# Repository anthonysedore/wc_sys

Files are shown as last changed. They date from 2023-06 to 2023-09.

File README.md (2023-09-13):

# wc_sys
Wireless Communication System for Electrathon





PCB designed in KiCad,

Code for ESP32 in Arduino

-read data from motor controller, battery BMS
-collect GPS data
-log all data to sdcard
-send data to pitcrew
-show important metrics and any warnings to driver
-enable recording cool videos with data synced to video time

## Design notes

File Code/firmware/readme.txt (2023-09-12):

freeRTOS and freeRTOS_geneisboard is the firmware going onto the board.
They should be combined but kept seperate for now, since pinout is different.

Do development in freeRTOS not freeRTOS_geneisboard

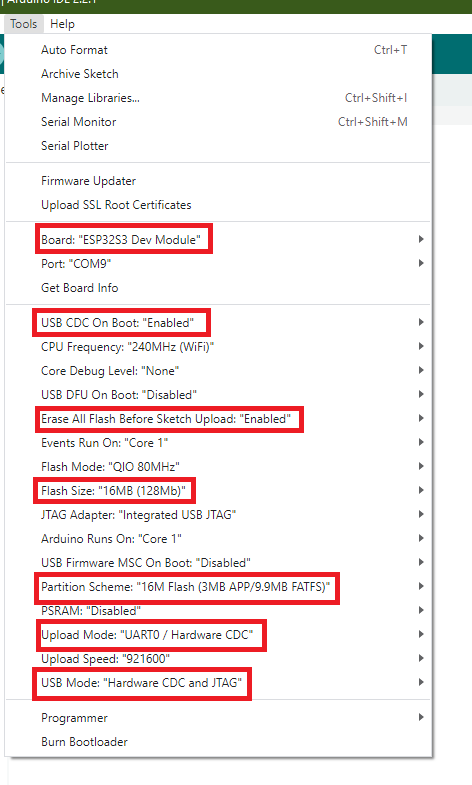
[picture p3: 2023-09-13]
Code/genesisboard.png

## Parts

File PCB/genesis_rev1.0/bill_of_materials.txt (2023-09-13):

"P/N	price	qty	description	notes"	
"PCB	26.9	5	from JLCPCB	"	
"MCP23008-E/SO-ND	$1.37 	1	IC XPNDR 1.7MHZ I2C 18SOIC	"	
"CP-43514-ND	$1.32 	1	CONN JACK 4COND 3.5MM R/A	""wrong jack for board"	" order new one"""
"497-5235-1-ND	$0.61 	1	TVS DIODE 5.25VWM 17VC SOT23-6	"	
"2073-USB4105-GF-ACT-ND	$0.81 	1	CONN RCP USB2.0 TYP C 24P SMD RA	"	
"EG4367-ND	$1.04 	1	SWITCH SLIDE DPDT 500MA 15V	"	
"PI4ULS5V202UEXDICT-ND	$0.76 	2	IC TRANSLTR BIDIRECTIONAL 8MSOP	"	
"DMG2301L-7DICT-ND	$0.33 	1	MOSFET P-CH 20V 3A SOT23	"	
"MCP73831T-2ACI/OTCT-ND	$0.76 	1	IC BATT CNTL LI-ION 1CEL SOT23-5	"	
"1965-ESP32-S3-WROOM-1U-N16R8CT-ND	$3.90 	1	RF TXRX MOD BLUETOOTH U.FL SMD	"
"hosyond3.5tft	$17	1	Hosyond 3.5 Inches TFT LCD Touch Screen	"
"neo-6m	$11	1	GPS Module GPS NEO-6M	"

about cost, $44 for a board
other parts that are not listed I had lying around should as resistors and capacitors, should document

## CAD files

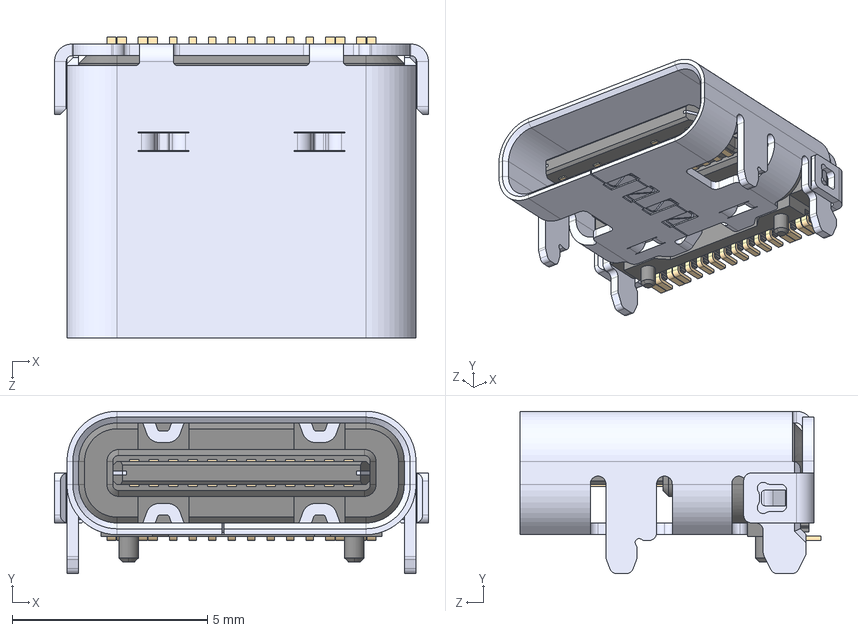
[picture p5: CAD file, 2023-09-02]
PCB/wc_sys_footprint/3dmodels/USB4105-GF-A.step
9.58 x 4.16 x 7.71 mm

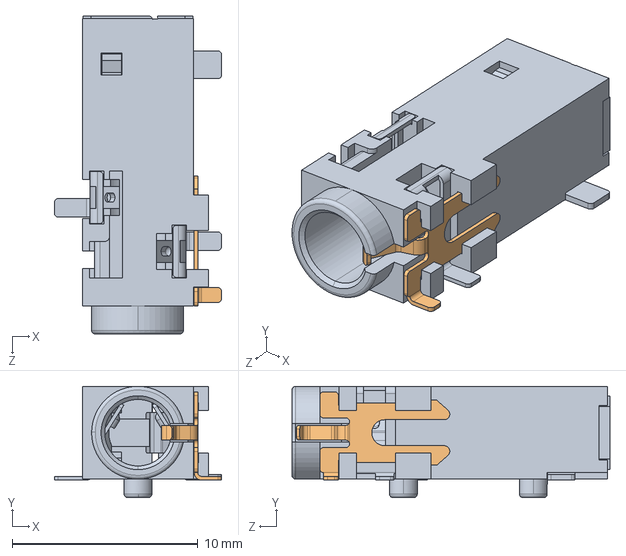
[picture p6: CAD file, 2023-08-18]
PCB/wc_sys_footprint/3dmodels/CUI_DEVICES_SJ-43514-SMT-TR.step
9.00 x 6.00 x 17.1 mm

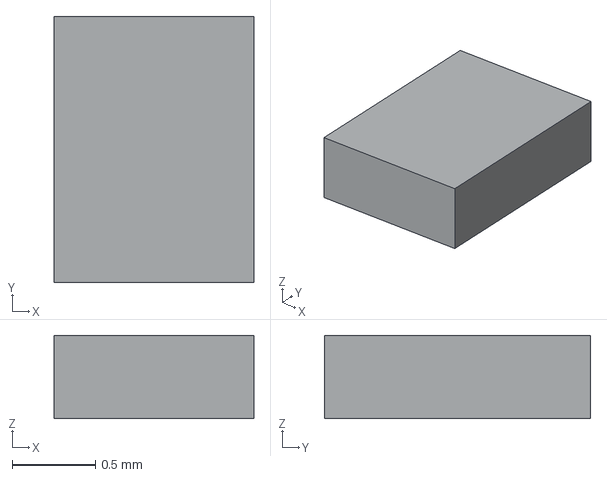
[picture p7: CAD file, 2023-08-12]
PCB/wc_sys_footprint/3dmodels/PI4ULS5V202XVEX.step
1.20 x 1.60 x 0.5 mm

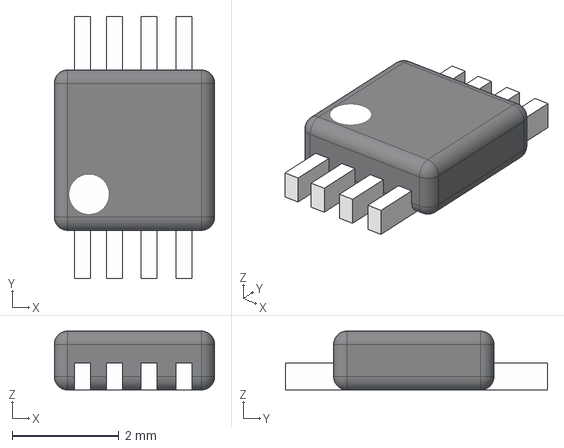
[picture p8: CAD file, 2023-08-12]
PCB/wc_sys_footprint/3dmodels/PI4ULS5V202UEX.step
3.00 x 4.90 x 1.10 mm

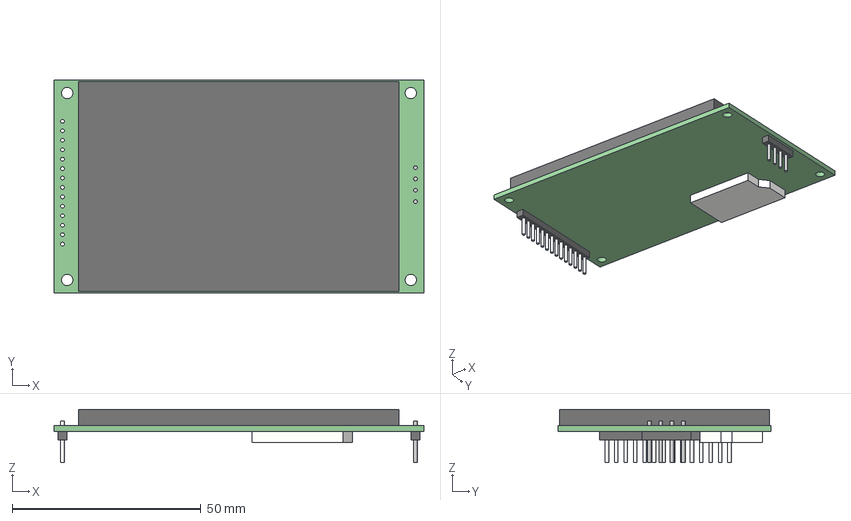
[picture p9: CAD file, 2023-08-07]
PCB/wc_sys_footprint/3dmodels/LCD Display.step
98.0 x 56.5 x 14.1 mm

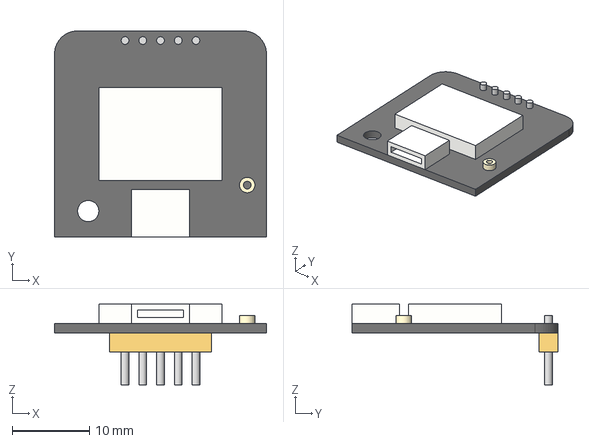
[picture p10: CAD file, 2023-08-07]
PCB/wc_sys_footprint/3dmodels/GT-U7GpsModule v1.step
27.5 x 26.8 x 10.5 mm

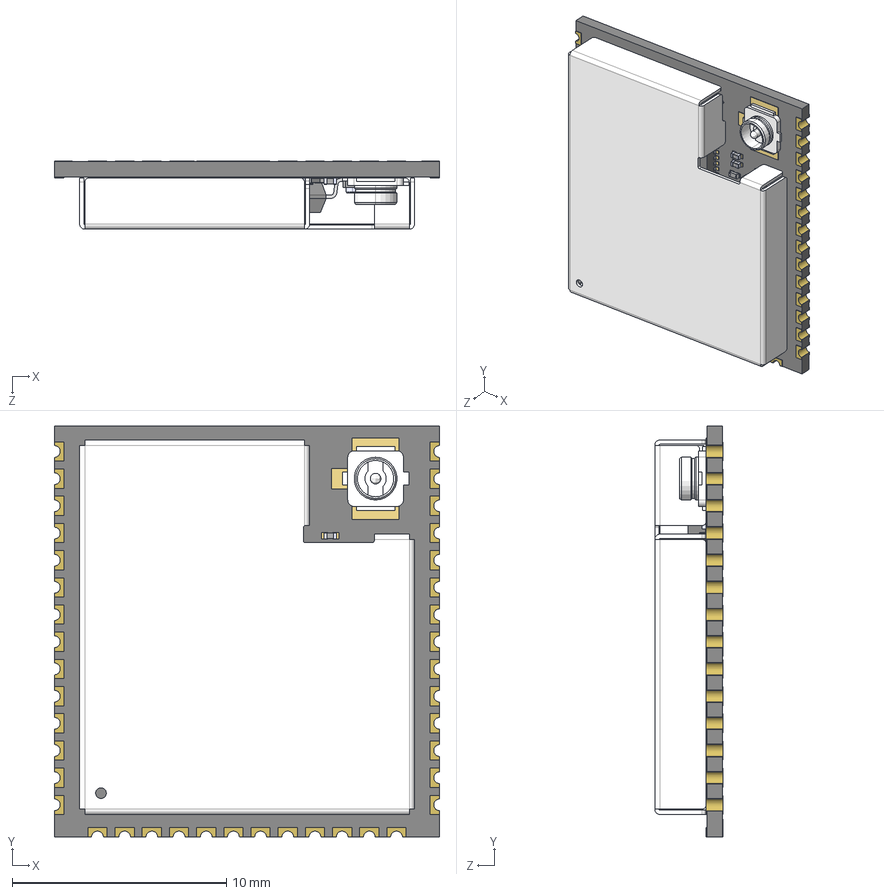
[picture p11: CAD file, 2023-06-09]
PCB/wc_sys_footprint/3dmodels/ESP32-S3-WROOM-1U.STEP
18.0 x 19.2 x 3.20 mm
R0201_20210301.STEP^R0201_20210301.STEP_Submodel-R0201_part_DesignRootModel_ESP32-S3-WROOM-1U(2)_ESP32-S3-WROOM-1U_2 x 8
L0201_20210301.STEP^L0201_20210301.STEP_Submodel-L0201_part_DesignRootModel_ESP32-S3-WROOM-1U(2)_ESP32-S3-WROOM-1U_2 x 2
C0201_20210301.STEP^C0201_20210301.STEP_Submodel-C0201_part_DesignRootModel_ESP32-S3-WROOM-1U(2)_ESP32-S3-WROOM-1U_2 x 13
C0402_20210301.STEP^C0402_20210301.STEP_Submodel-C0402_part_DesignRootModel_ESP32-S3-WROOM-1U(2)_ESP32-S3-WROOM-1U_2
I-IPEX.STEP^I-IPEX.STEP_Submodel-IPEX_3P_part_DesignRootModel_ESP32-S3-WROOM-1U(2)_ESP32-S3-WROOM-1U_2
DFN1006.STEP^DFN1006.STEP_Submodel-SOD882_part_DesignRootModel_ESP32-S3-WROOM-1U(2)_ESP32-S3-WROOM-1U_2
SOP8_rev1_20210308.STEP^SOP8_rev1_20210308.STEP_Submodel-SOP8_1P27_6P6_part_DesignRootModel_ESP32-S3-WROOM-1U(2)_ESP32-S3-WROOM-1U_2
ESP32-S3_20210301.STEP^ESP32-S3_20210301.STEP_Submodel-QFN56_0P4_7_part_DesignRootModel_ESP32-S3-WROOM-1U(2)_ESP32-S3-WROOM-1U_2
XTAL3225_20210301.STEP^XTAL3225_20210301.STEP_Submodel-XTAL3225_part_DesignRootModel_ESP32-S3-WROOM-1U(2)_ESP32-S3-WROOM-1U_2
uid__4-111^DesignRootModel_ESP32-S3-WROOM-1U(2)_ESP32-S3-WROOM-1U_2
uid__4-112^DesignRootModel_ESP32-S3-WROOM-1U(2)_ESP32-S3-WROOM-1U_2
uid__4-113^DesignRootModel_ESP32-S3-WROOM-1U(2)_ESP32-S3-WROOM-1U_2
uid__4-130^DesignRootModel_ESP32-S3-WROOM-1U(2)_ESP32-S3-WROOM-1U_2
uid__4-131^DesignRootModel_ESP32-S3-WROOM-1U(2)_ESP32-S3-WROOM-1U_2
uid__4-132^DesignRootModel_ESP32-S3-WROOM-1U(2)_ESP32-S3-WROOM-1U_2
uid__4-148^DesignRootModel_ESP32-S3-WROOM-1U(2)_ESP32-S3-WROOM-1U_2
uid__4-149^DesignRootModel_ESP32-S3-WROOM-1U(2)_ESP32-S3-WROOM-1U_2
uid__4-150^DesignRootModel_ESP32-S3-WROOM-1U(2)_ESP32-S3-WROOM-1U_2
uid__1-253^DesignRootModel_ESP32-S3-WROOM-1U(2)_ESP32-S3-WROOM-1U_2
uid__1-254^DesignRootModel_ESP32-S3-WROOM-1U(2)_ESP32-S3-WROOM-1U_2
uid__1-256^DesignRootModel_ESP32-S3-WROOM-1U(2)_ESP32-S3-WROOM-1U_2
uid__1-257^DesignRootModel_ESP32-S3-WROOM-1U(2)_ESP32-S3-WROOM-1U_2
uid__1-266^DesignRootModel_ESP32-S3-WROOM-1U(2)_ESP32-S3-WROOM-1U_2
uid__1-269^DesignRootModel_ESP32-S3-WROOM-1U(2)_ESP32-S3-WROOM-1U_2
uid__1-270^DesignRootModel_ESP32-S3-WROOM-1U(2)_ESP32-S3-WROOM-1U_2
uid__1-271^DesignRootModel_ESP32-S3-WROOM-1U(2)_ESP32-S3-WROOM-1U_2
uid__1-272^DesignRootModel_ESP32-S3-WROOM-1U(2)_ESP32-S3-WROOM-1U_2
uid__1-273^DesignRootModel_ESP32-S3-WROOM-1U(2)_ESP32-S3-WROOM-1U_2
uid__1-274^DesignRootModel_ESP32-S3-WROOM-1U(2)_ESP32-S3-WROOM-1U_2
uid__1-275^DesignRootModel_ESP32-S3-WROOM-1U(2)_ESP32-S3-WROOM-1U_2
uid__1-276^DesignRootModel_ESP32-S3-WROOM-1U(2)_ESP32-S3-WROOM-1U_2
uid__1-277^DesignRootModel_ESP32-S3-WROOM-1U(2)_ESP32-S3-WROOM-1U_2
uid__1-280^DesignRootModel_ESP32-S3-WROOM-1U(2)_ESP32-S3-WROOM-1U_2
uid__1-292^DesignRootModel_ESP32-S3-WROOM-1U(2)_ESP32-S3-WROOM-1U_2
uid__1-293^DesignRootModel_ESP32-S3-WROOM-1U(2)_ESP32-S3-WROOM-1U_2
uid__1-297^DesignRootModel_ESP32-S3-WROOM-1U(2)_ESP32-S3-WROOM-1U_2
uid__1-300^DesignRootModel_ESP32-S3-WROOM-1U(2)_ESP32-S3-WROOM-1U_2
uid__1-301^DesignRootModel_ESP32-S3-WROOM-1U(2)_ESP32-S3-WROOM-1U_2
uid__1-302^DesignRootModel_ESP32-S3-WROOM-1U(2)_ESP32-S3-WROOM-1U_2
uid__1-303^DesignRootModel_ESP32-S3-WROOM-1U(2)_ESP32-S3-WROOM-1U_2
uid__1-307^DesignRootModel_ESP32-S3-WROOM-1U(2)_ESP32-S3-WROOM-1U_2
uid__1-313^DesignRootModel_ESP32-S3-WROOM-1U(2)_ESP32-S3-WROOM-1U_2
uid__1-319^DesignRootModel_ESP32-S3-WROOM-1U(2)_ESP32-S3-WROOM-1U_2
uid__1-320^DesignRootModel_ESP32-S3-WROOM-1U(2)_ESP32-S3-WROOM-1U_2
uid__1-321^DesignRootModel_ESP32-S3-WROOM-1U(2)_ESP32-S3-WROOM-1U_2
uid__1-328^DesignRootModel_ESP32-S3-WROOM-1U(2)_ESP32-S3-WROOM-1U_2
uid__1-332^DesignRootModel_ESP32-S3-WROOM-1U(2)_ESP32-S3-WROOM-1U_2
uid__1-333^DesignRootModel_ESP32-S3-WROOM-1U(2)_ESP32-S3-WROOM-1U_2
uid__1-334^DesignRootModel_ESP32-S3-WROOM-1U(2)_ESP32-S3-WROOM-1U_2
uid__1-335^DesignRootModel_ESP32-S3-WROOM-1U(2)_ESP32-S3-WROOM-1U_2
uid__1-336^DesignRootModel_ESP32-S3-WROOM-1U(2)_ESP32-S3-WROOM-1U_2
uid__1-337^DesignRootModel_ESP32-S3-WROOM-1U(2)_ESP32-S3-WROOM-1U_2
uid__1-338^DesignRootModel_ESP32-S3-WROOM-1U(2)_ESP32-S3-WROOM-1U_2
uid__1-339^DesignRootModel_ESP32-S3-WROOM-1U(2)_ESP32-S3-WROOM-1U_2
uid__1-340^DesignRootModel_ESP32-S3-WROOM-1U(2)_ESP32-S3-WROOM-1U_2
uid__1-341^DesignRootModel_ESP32-S3-WROOM-1U(2)_ESP32-S3-WROOM-1U_2
uid__1-342^DesignRootModel_ESP32-S3-WROOM-1U(2)_ESP32-S3-WROOM-1U_2
uid__1-343^DesignRootModel_ESP32-S3-WROOM-1U(2)_ESP32-S3-WROOM-1U_2
uid__1-344^DesignRootModel_ESP32-S3-WROOM-1U(2)_ESP32-S3-WROOM-1U_2
uid__1-345^DesignRootModel_ESP32-S3-WROOM-1U(2)_ESP32-S3-WROOM-1U_2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

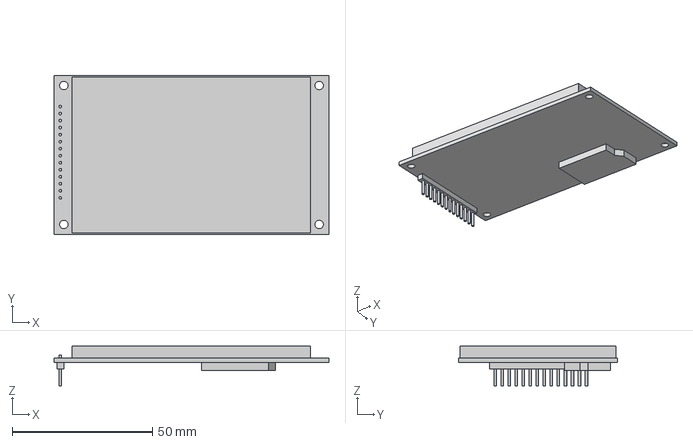
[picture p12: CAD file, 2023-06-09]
PCB/wc_sys_footprint/3dmodels/3.5 TFI SPI 480X320 V1 v3.step
98.0 x 56.5 x 14.1 mm

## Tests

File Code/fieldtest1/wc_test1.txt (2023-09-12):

csv file is direct output from SDcard mounted in unit.
Video created in racerender using gopro video and csv file output.
-------
set gps sample rate higher
fix crash when gps doesn't pick up satelite and try to start recording
improve time syncronization instead of relying on delays

investigate if SDcard should go on seperate SPI controller on esp32

Add GOPRO control feature to start and stop recording automatically

--------------------
Update: gps sample rate and fixed time sync.

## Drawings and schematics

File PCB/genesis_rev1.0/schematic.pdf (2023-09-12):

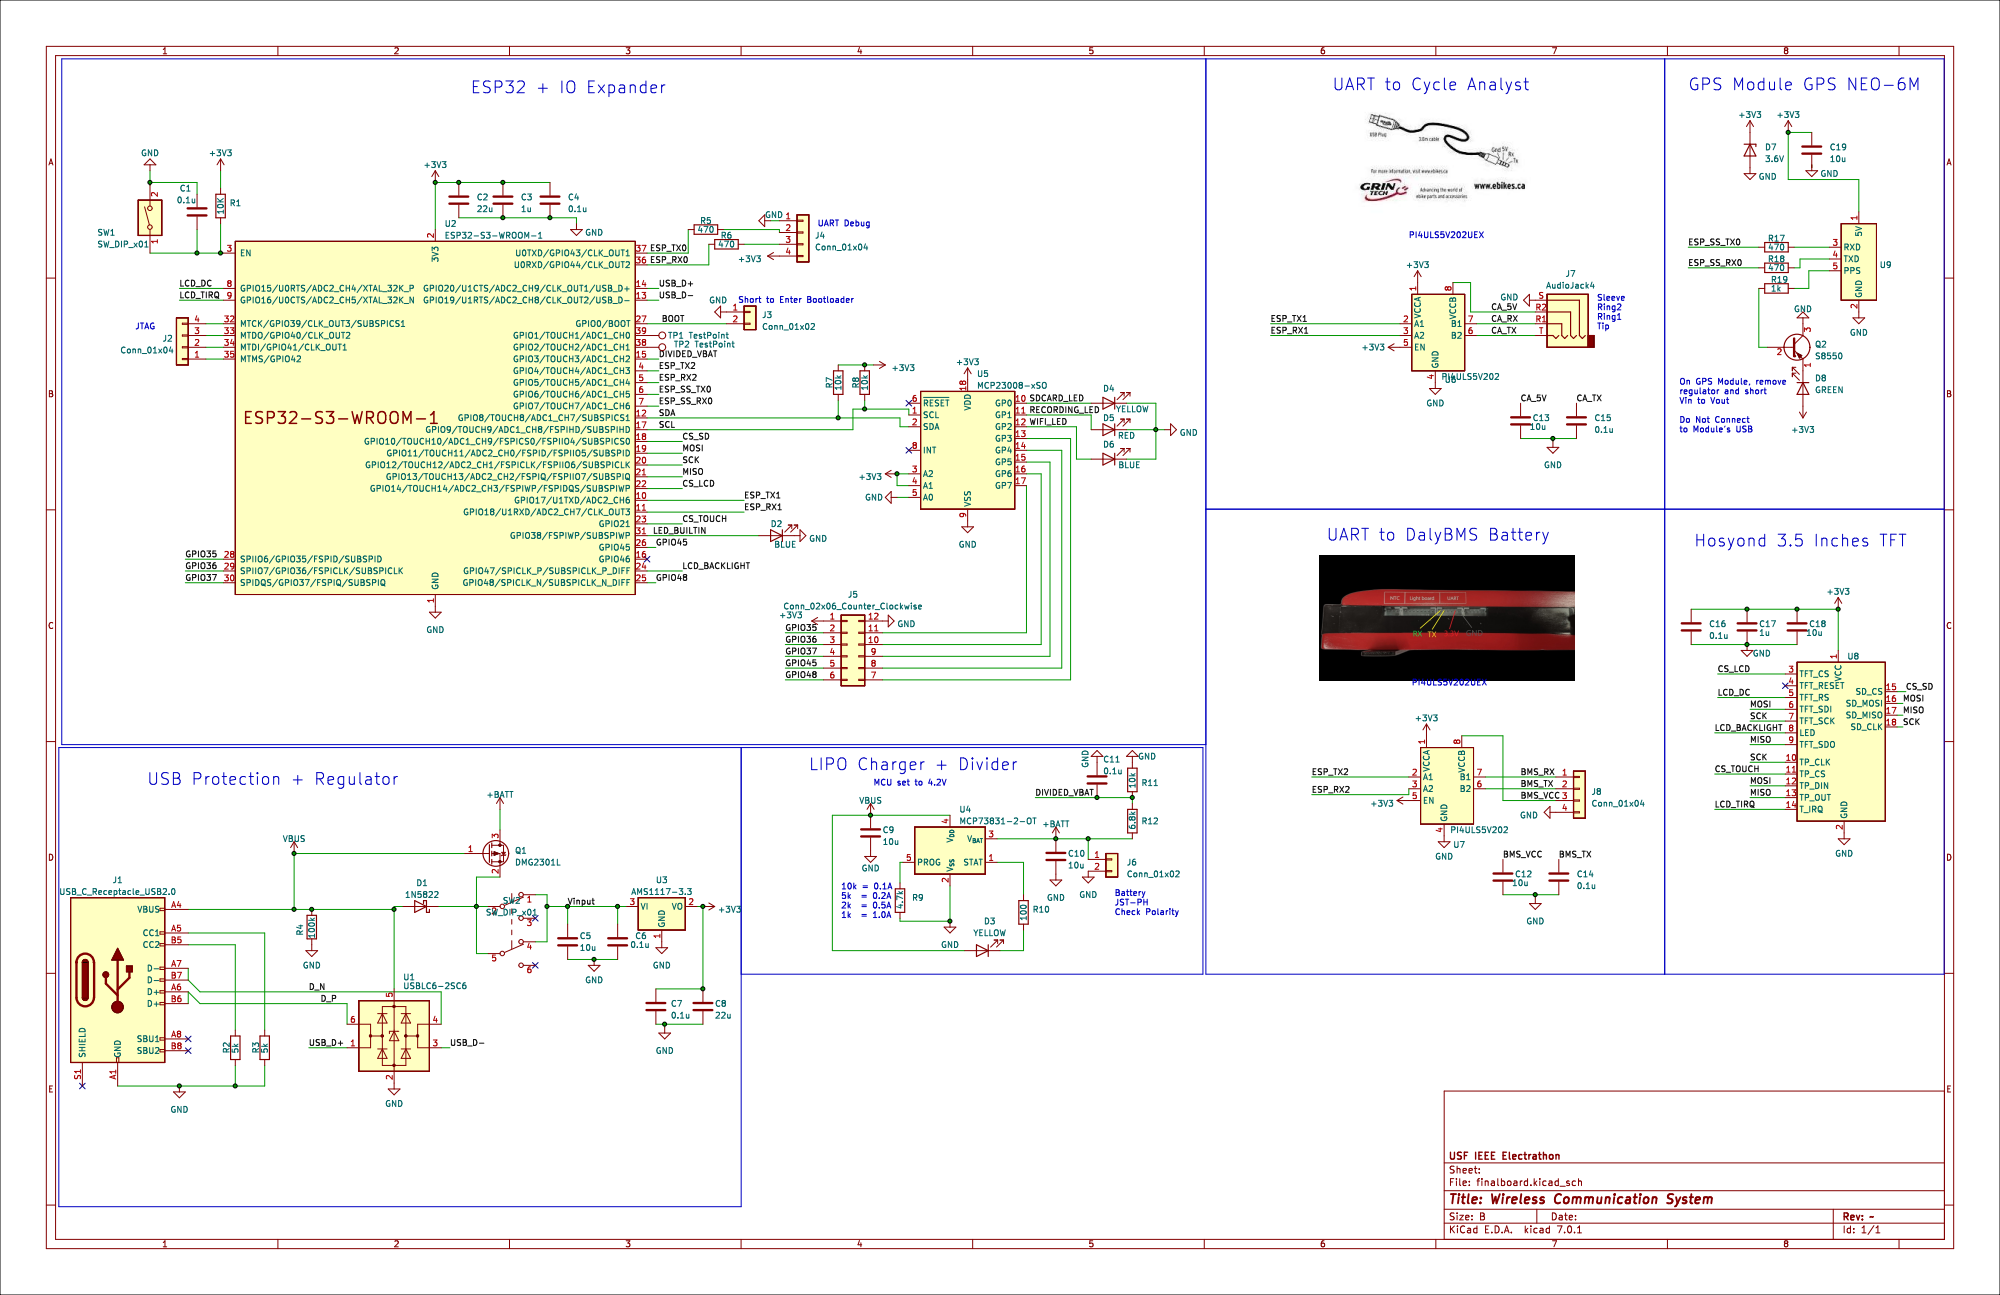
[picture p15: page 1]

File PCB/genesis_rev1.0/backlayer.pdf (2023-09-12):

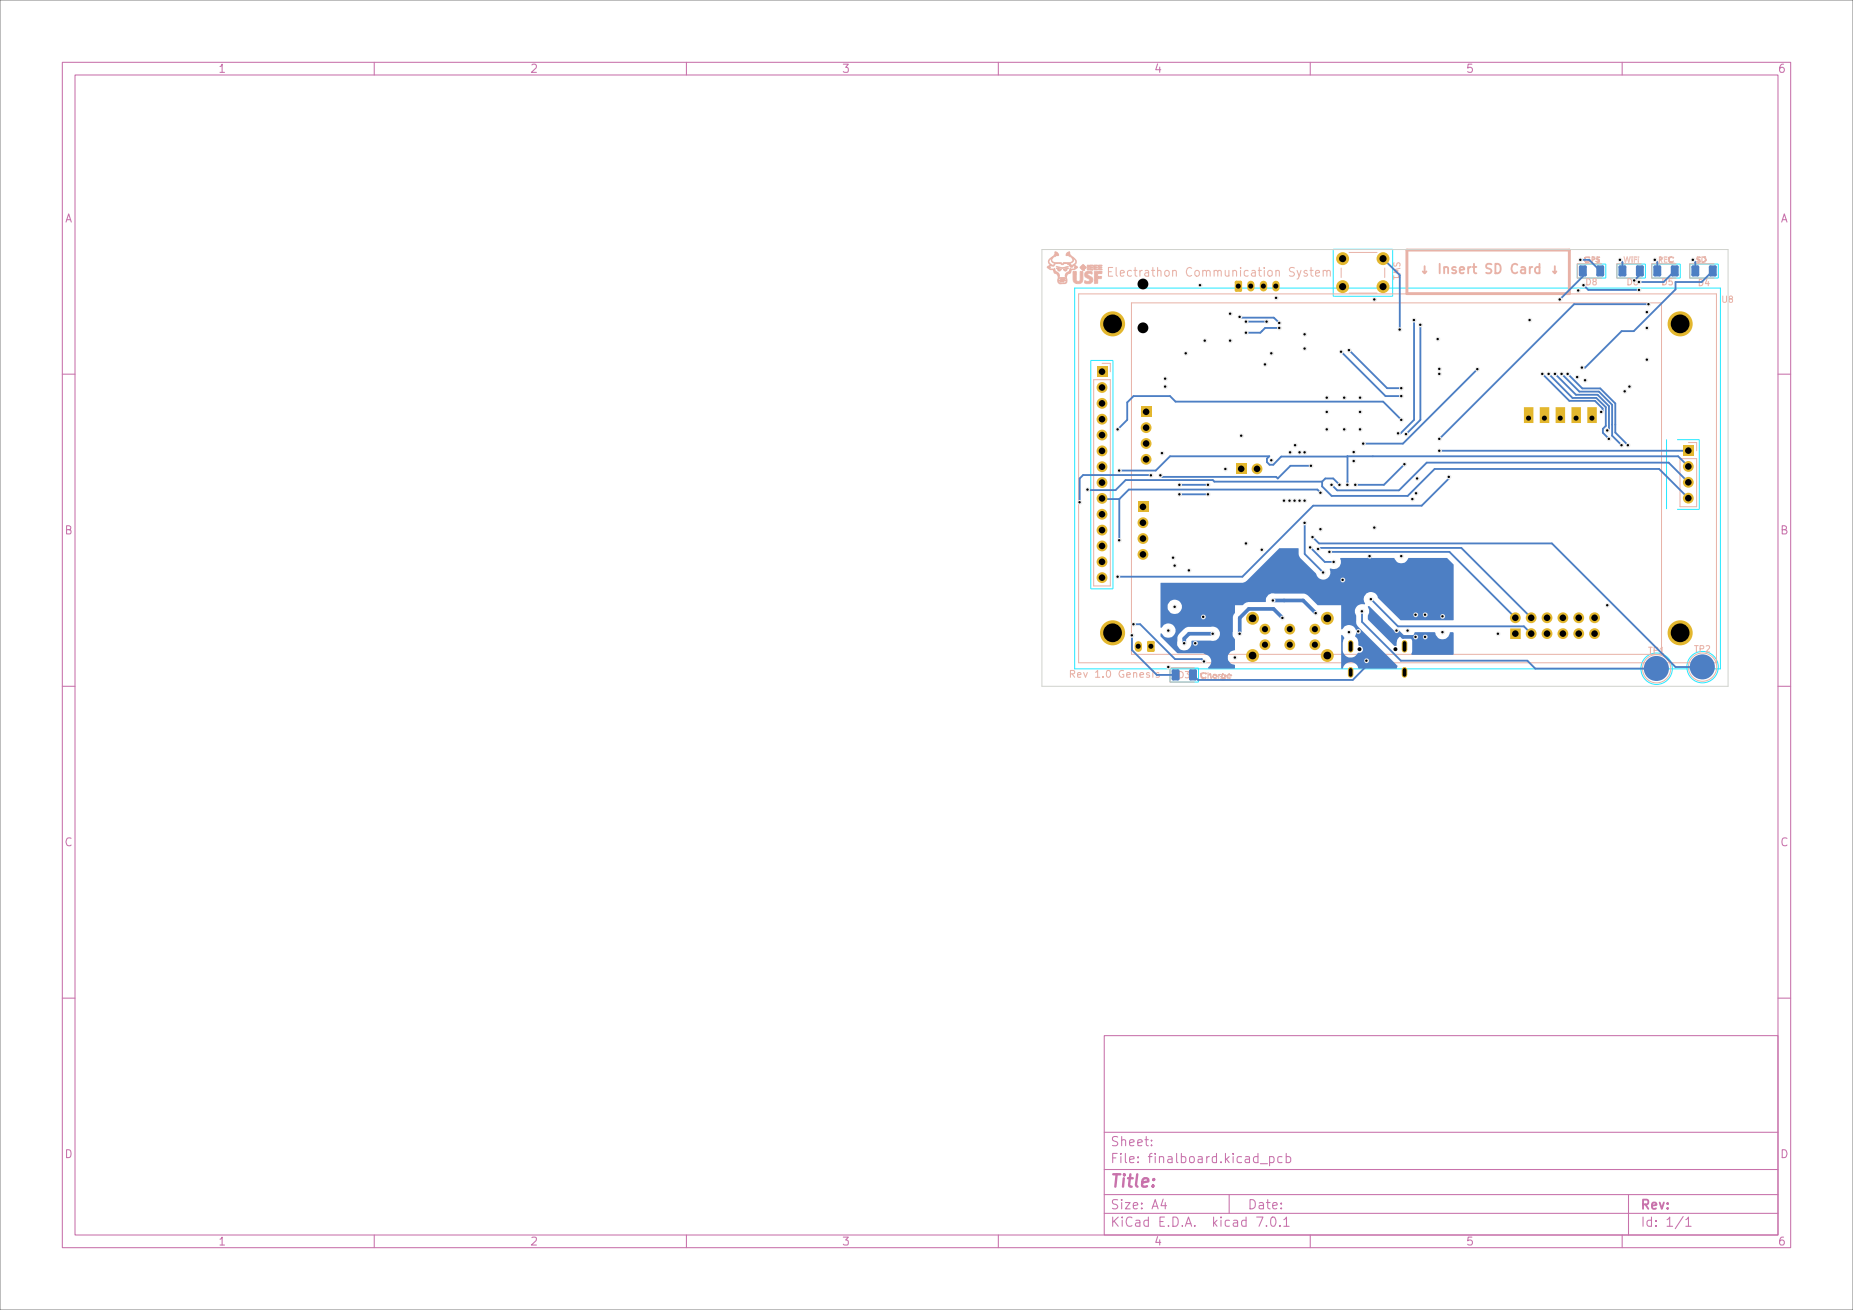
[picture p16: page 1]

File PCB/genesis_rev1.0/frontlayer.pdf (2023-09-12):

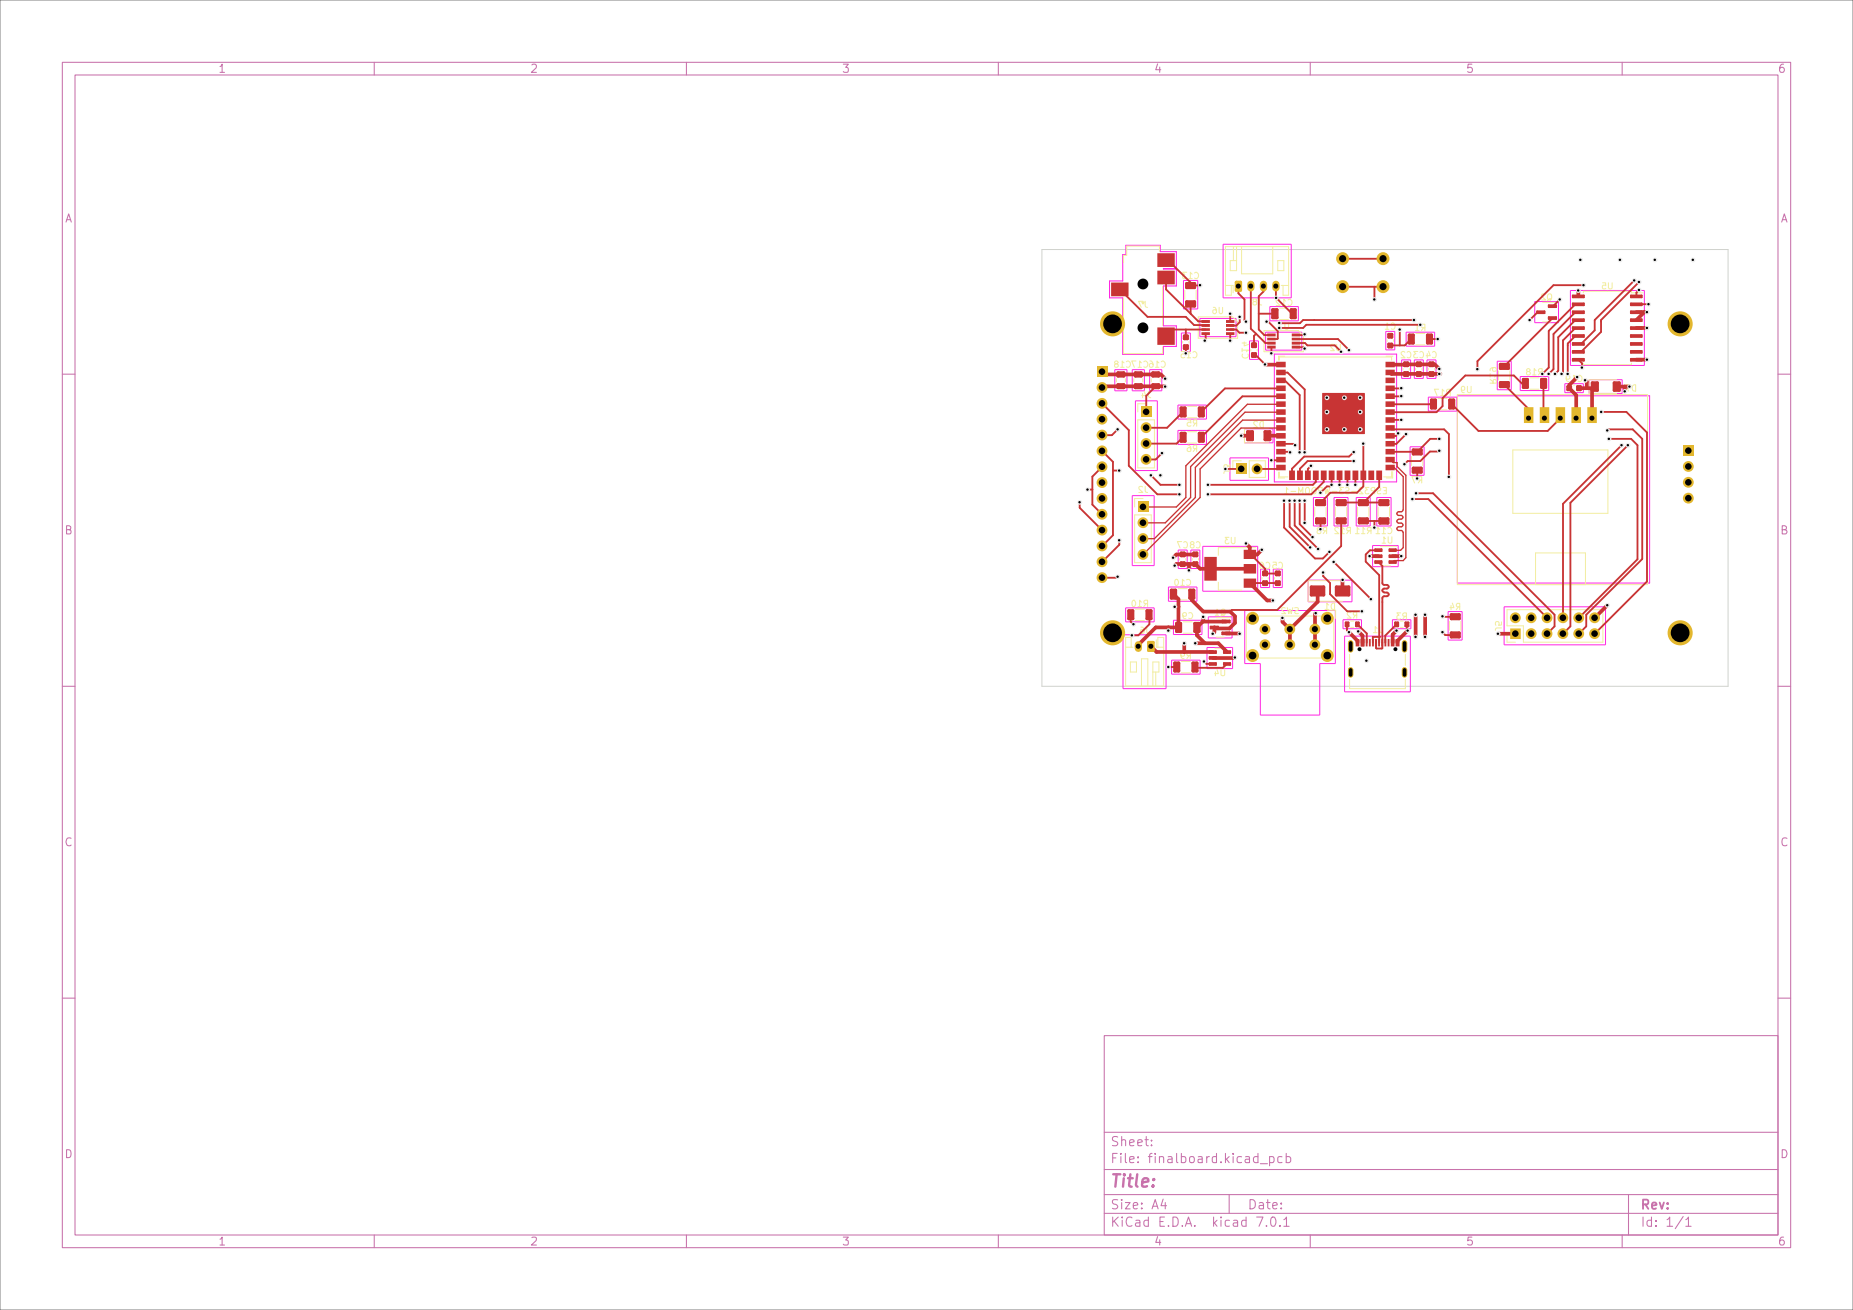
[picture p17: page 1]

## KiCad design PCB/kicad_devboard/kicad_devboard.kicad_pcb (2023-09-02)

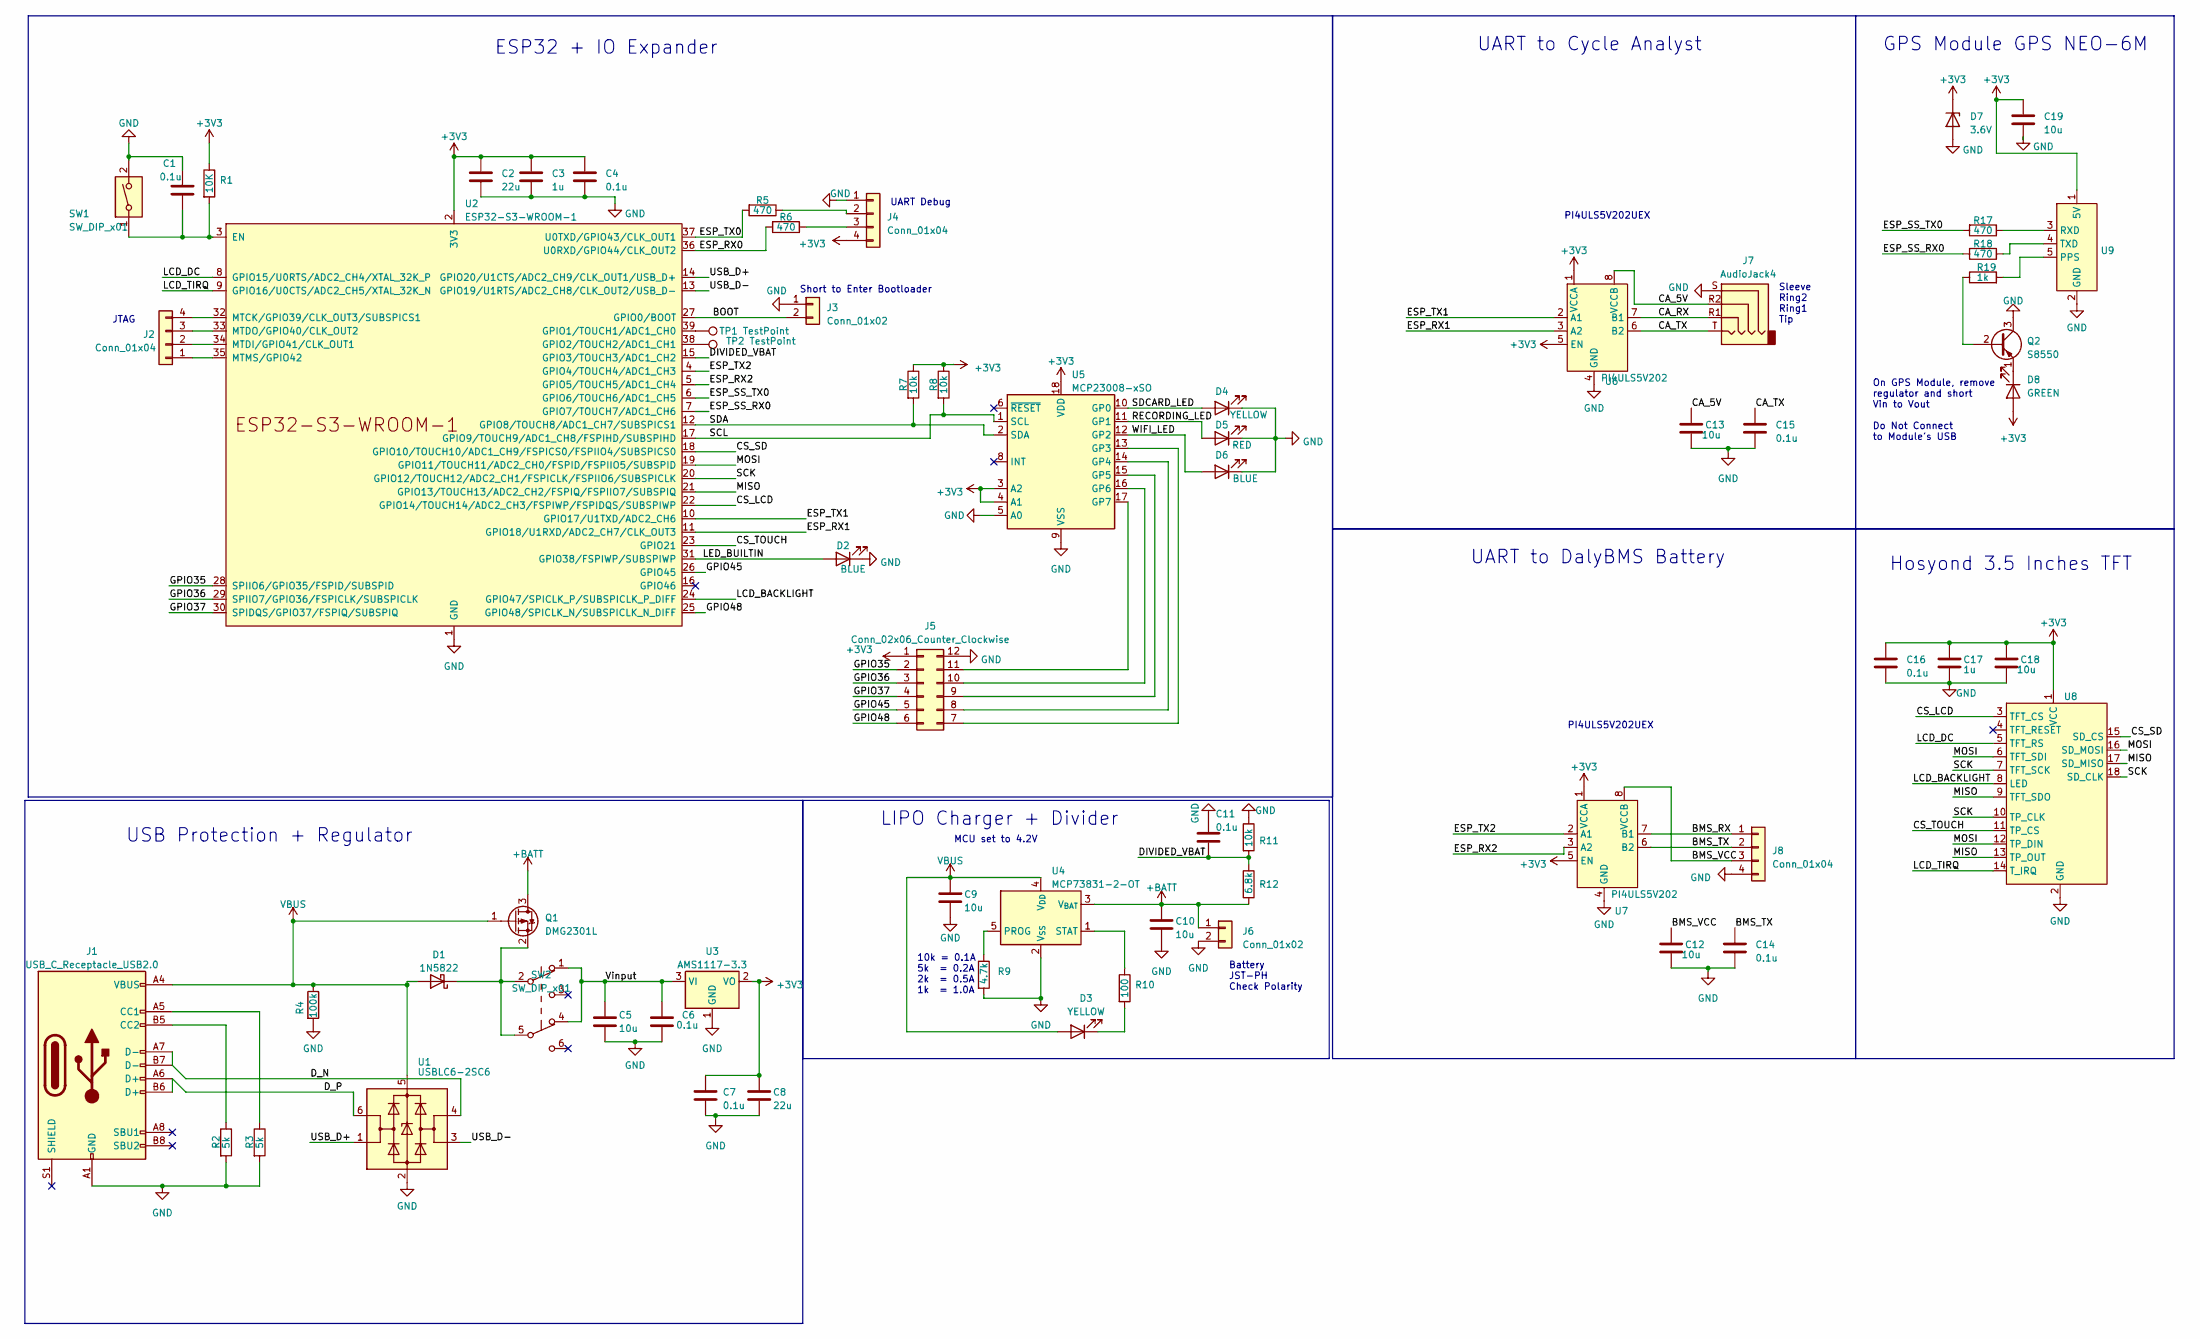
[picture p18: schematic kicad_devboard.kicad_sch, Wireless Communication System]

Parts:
C1, C4, C6, C7, C14, C15: 0.1u; C_0603_1608Metric
C2, C8: 22u; C_0603_1608Metric
C3: 1u; C_0603_1608Metric
C5, C19: 10u; C_0603_1608Metric
C9, C10, C12, C13: 10u; C_1206_3216Metric
C11: 0.1u; C_1206_3216Metric
C16: 0.1u; C_0805_2012Metric
C17: 1u; C_0805_2012Metric
C18: 10u; C_0805_2012Metric
D1: 1N5822; D_SMA
D2, D6: BLUE; LED_1206_3216Metric
D3, D4: YELLOW; LED_1206_3216Metric
D5: RED; LED_1206_3216Metric
D7: 3.6V; D_MiniMELF
D8: GREEN; LED_1206_3216Metric
J1: USB_C_Receptacle_USB2.0; USB_C_Receptacle_Palconn_UTC16-G
J2, J4: Conn_01x04; PinSocket_1x04_P2.54mm_Vertical
J3: Conn_01x02; PinHeader_1x02_P2.54mm_Vertical
J5: Conn_02x06_Counter_Clockwise; PinSocket_2x06_P2.54mm_Vertical
J6: Conn_01x02; JST_PH_S2B-PH-K_1x02_P2.00mm_Horizontal
J7: AudioJack4; SJ-43514-SMT_CUD
J8: Conn_01x04; JST_PH_S4B-PH-K_1x04_P2.00mm_Horizontal
Q1: DMG2301L; SOT-23
Q2: S8550; SOT-23
R1: 10K; R_1206_3216Metric
R2, R3: 5k; R_0603_1608Metric
R4: 100k; R_1206_3216Metric
R5, R6, R17, R18: 470; R_1206_3216Metric
R7, R8, R11: 10k; R_1206_3216Metric
R9: 4.7k; R_1206_3216Metric
R10: 100; R_1206_3216Metric
R12: 6.8k; R_1206_3216Metric
R19: 1k; R_1206_3216Metric
SW1: SW_DIP_x01; SW_PUSH_6mm_H5mm
SW2: SW_DIP_x01; SW_E-Switch_EG2219_DPDT_Angled
TP1, TP2: TestPoint; TestPoint_Pad_D4.0mm
U1: USBLC6-2SC6; SOT-23-6
U2: ESP32-S3-WROOM-1; ESP32-S3-WROOM-1U
U3: AMS1117-3.3; SOT-223-3_TabPin2
U4: MCP73831-2-OT; SOT-23-5
U5: MCP23008-xSO; SOIC-18W_7.5x11.6mm_P1.27mm
U6, U7: PI4ULS5V202; PI4ULS5V202UEX
U8: 3.5_inch_SPI_Module_ILI9488
U9: GT-U7

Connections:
+3V3: C2.1, C3.1, C4.1, C7.1, C8.1, C16.1, C17.1, C18.1, C19.1, D7.1 (K), D8.2 (A), J4.4, J5.1, R1.1, R7.1, R8.1, U2.2 (3V3), U3.2 (VO), U5.3 (A2), U5.4 (A1), U5.18 (VDD), U6.1 (VCCA), U6.5 (EN), U7.1 (VCCA), U7.5 (EN), U8.1 (VCC), U9.1 (5V)
+BATT: C10.1, J6.1, Q1.3 (D), R12.2, U4.3 (V_{BAT})
/BMS_RX: J8.1, U7.7 (B1)
/BMS_TX: C14.1, J8.2, U7.6 (B2)
/BMS_VCC: C12.1, J8.3, U7.8 (VCCB)
/BOOT: J3.2, U2.27 (GPIO0/BOOT)
/CA_5V: C13.1, J7.R2, U6.8 (VCCB)
/CA_RX: J7.R1, U6.7 (B1)
/CA_TX: C15.1, J7.T, U6.6 (B2)
/CS_LCD: U2.22 (GPIO14/TOUCH14/ADC2_CH3/FSPIWP/FSPIDQS/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), U8.3 (TFT_CS)
/CS_SD: U2.18 (GPIO10/TOUCH10/ADC1_CH9/FSPICS0/FSPIIO4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), U8.15 (SD_CS)
/CS_TOUCH: U2.23 (GPIO21), U8.11 (TP_CS)
/DIVIDED_VBAT: C11.2, R11.2, R12.1, U2.15 (GPIO3/TOUCH3/ADC1_CH2)
/ESP_RX0: R6.2, U2.36 (U0RXD/GPIO44/CLK_OUT2)
/ESP_RX1: U2.11 (GPIO18/U1RXD/ADC2_CH7/CLK_OUT3), U6.3 (A2)
/ESP_RX2: U2.5 (GPIO5/TOUCH5/ADC1_CH4), U7.3 (A2)
/ESP_SS_RX0: R18.2, U2.7 (GPIO7/TOUCH7/ADC1_CH6)
/ESP_SS_TX0: R17.2, U2.6 (GPIO6/TOUCH6/ADC1_CH5)
/ESP_TX0: R5.2, U2.37 (U0TXD/GPIO43/CLK_OUT1)
/ESP_TX1: U2.10 (GPIO17/U1TXD/ADC2_CH6), U6.2 (A1)
/ESP_TX2: U2.4 (GPIO4/TOUCH4/ADC1_CH3), U7.2 (A1)
/GPIO35: J5.2, U2.28 (SPIIO6/GPIO35/FSPID/SUBSPID)
/GPIO36: J5.3, U2.29 (SPIIO7/GPIO36/FSPICLK/SUBSPICLK)
/GPIO37: J5.4, U2.30 (SPIDQS/GPIO37/FSPIQ/SUBSPIQ)
/GPIO45: J5.5, U2.26 (GPIO45)
/GPIO48: J5.6, U2.25 (GPIO48/SPICLK_N/SUBSPICLK_N_DIFF)
/LCD_BACKLIGHT: U2.24 (GPIO47/SPICLK_P/SUBSPICLK_P_DIFF), U8.8 (LED)
/LCD_DC: U2.8 (GPIO15/U0RTS/ADC2_CH4/XTAL_32K_P), U8.5 (TFT_RS)
/LCD_TIRQ: U2.9 (GPIO16/U0CTS/ADC2_CH5/XTAL_32K_N), U8.14 (T_IRQ)
/LED_BUILTIN: D2.2 (A), U2.31 (GPIO38/FSPIWP/SUBSPIWP)
/MISO: U2.21 (GPIO13/TOUCH13/ADC2_CH2/FSPIQ/FSPIIO7/S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), U8.9 (TFT_SDO), U8.13 (TP_OUT), U8.17 (SD_MISO)
/MOSI: U2.19 (GPIO11/TOUCH11/ADC2_CH0/FSPID/FSPIIO5/S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), U8.6 (TFT_SDI), U8.12 (TP_DIN), U8.16 (SD_MOSI)
/RECORDING_LED: D5.2 (A), U5.11 (GP1)
/SCK: U2.20 (GPIO12/TOUCH12/ADC2_CH1/FSPICLK/FSPIIO6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), U8.7 (TFT_SCK), U8.10 (TP_CLK), U8.18 (SD_CLK)
/SCL: R8.2, U2.17 (GPIO9/TOUCH9/ADC1_CH8/FSPIHD/SUBSPIHD), U5.1 (SCL)
/SDA: R7.2, U2.12 (GPIO8/TOUCH8/ADC1_CH7/SUBSPICS1), U5.2 (SDA)
/SDCARD_LED: D4.2 (A), U5.10 (GP0)
/USB_D+: U1.1 (I/O1), U2.14 (GPIO20/U1CTS/ADC2_CH9/CLK_OUT1/USB_D+)
/USB_D-: U1.3 (I/O2), U2.13 (GPIO19/U1RTS/ADC2_CH8/CLK_OUT2/USB_D-)
/Vinput: C5.1, C6.2, SW2.1 (A), SW2.4 (A), U3.3 (VI)
/WIFI_LED: D6.2 (A), U5.12 (GP2)
GND: C1.1, C2.2, C3.2, C4.2, C5.2, C6.1, C7.2, C8.2, C9.2, C10.2, C11.1, C12.2, C13.2, C14.2, C15.2, C16.2, C17.2, C18.2, C19.2, D2.1 (K), D4.1 (K), D5.1 (K), D6.1 (K), D7.2 (A), J1.A1 (GND), J1.A12 (GND), J1.B1 (GND), J1.B12 (GND), J3.1, J4.1, J5.12, J6.2, J7.S, J8.4, Q2.3 (C), R2.2, R3.2, R4.2, R9.2, R11.1, SW1.2, U1.2 (GND), U2.1 (GND), U2.40 (GND), U2.41 (GND), U3.1 (GND), U4.2 (V_{SS}), U5.5 (A0), U5.9 (VSS), U6.4 (GND), U7.4 (GND), U8.2 (GND), U9.2 (GND)
unnamed: D1.1 (K), Q1.2 (S), SW2.2 (B), SW2.5 (B)
unnamed: D3.1 (K), R10.2
unnamed: D8.1 (K), Q2.1 (E)
unnamed: J1.A5 (CC1), R3.1
unnamed: J1.B5 (CC2), R2.1
unnamed: J2.1, U2.35 (MTMS/GPIO42)
unnamed: J2.2, U2.34 (MTDI/GPIO41/CLK_OUT1)
unnamed: J2.3, U2.33 (MTDO/GPIO40/CLK_OUT2)
unnamed: J2.4, U2.32 (MTCK/GPIO39/CLK_OUT3/SUBSPICS1)
unnamed: J4.2, R5.1
unnamed: J4.3, R6.1
unnamed: J5.7, U5.13 (GP3)
unnamed: J5.8, U5.14 (GP4)
unnamed: J5.9, U5.15 (GP5)
unnamed: J5.10, U5.16 (GP6)
unnamed: J5.11, U5.17 (GP7)
unnamed: Q2.2 (B), R19.1
unnamed: C1.2, R1.2, SW1.1, U2.3 (EN)
unnamed: TP1.1, U2.39 (GPIO1/TOUCH1/ADC1_CH0)
unnamed: TP2.1, U2.38 (GPIO2/TOUCH2/ADC1_CH1)
unnamed: R9.1, U4.5 (PROG)
unnamed: R10.1, U4.1 (STAT)
unnamed: R19.2, U9.5 (PPS)
unnamed: R17.1, U9.3 (RXD)
unnamed: R18.1, U9.4 (TXD)
VBUS: C9.1, D1.2 (A), D3.2 (A), J1.A4 (VBUS), J1.A9 (VBUS), J1.B4 (VBUS), J1.B9 (VBUS), Q1.1 (G), R4.1, U1.5 (VBUS), U4.4 (V_{DD})

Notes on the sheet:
UART to DalyBMS Battery
Hosyond 3.5 Inches TFT
10k = 0.1A 5k = 0.2A 2k = 0.5A 1k = 1.0A
PI4ULS5V202UEX
USB Protection + Regulator
UART Debug
On GPS Module, remove regulator and short Vin to Vout Do Not Connect to Module's USB
GPS Module GPS NEO-6M
LIPO Charger + Divider
ESP32 + IO Expander
UART to Cycle Analyst
JTAG
Sleeve Ring2 Ring1 Tip
MCU set to 4.2V
Battery JST-PH Check Polarity
Short to Enter Bootloader

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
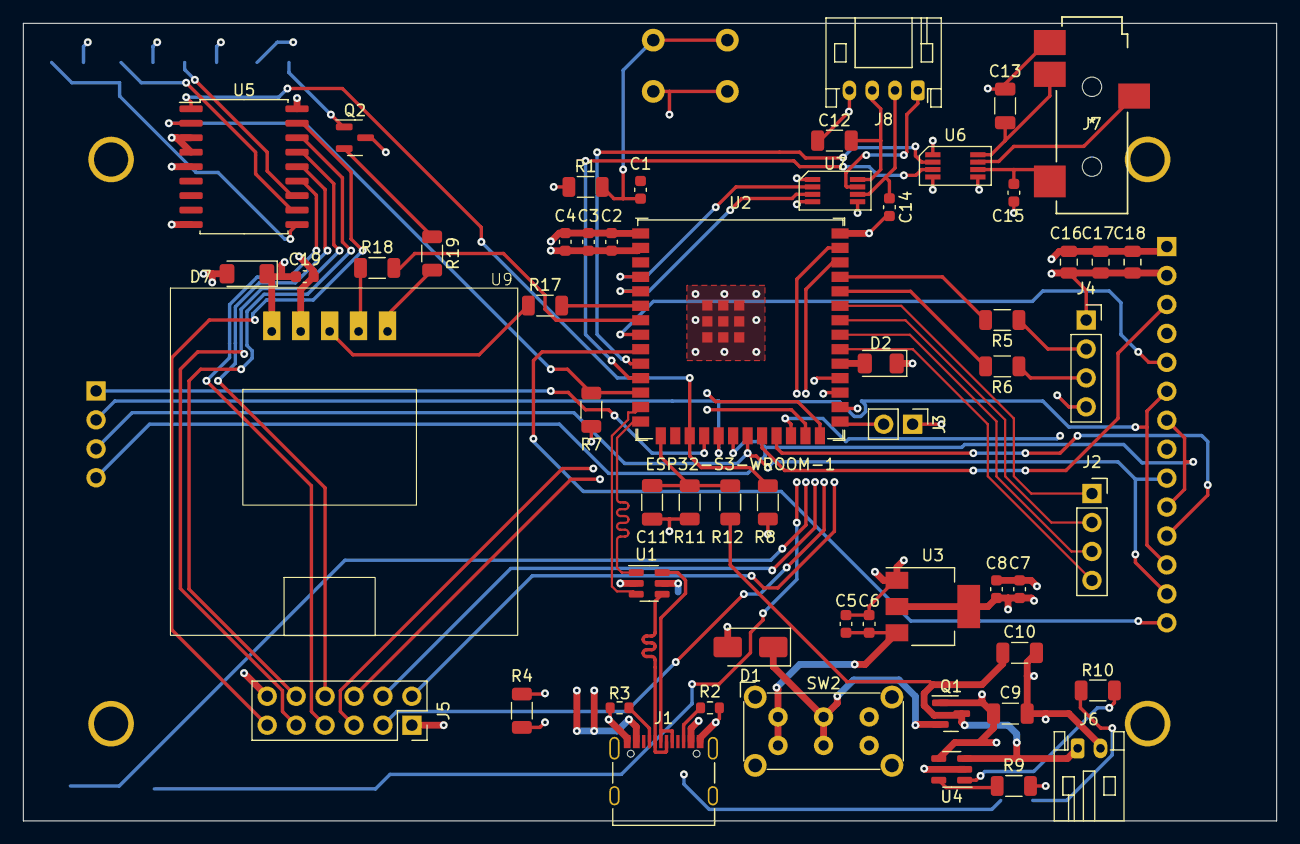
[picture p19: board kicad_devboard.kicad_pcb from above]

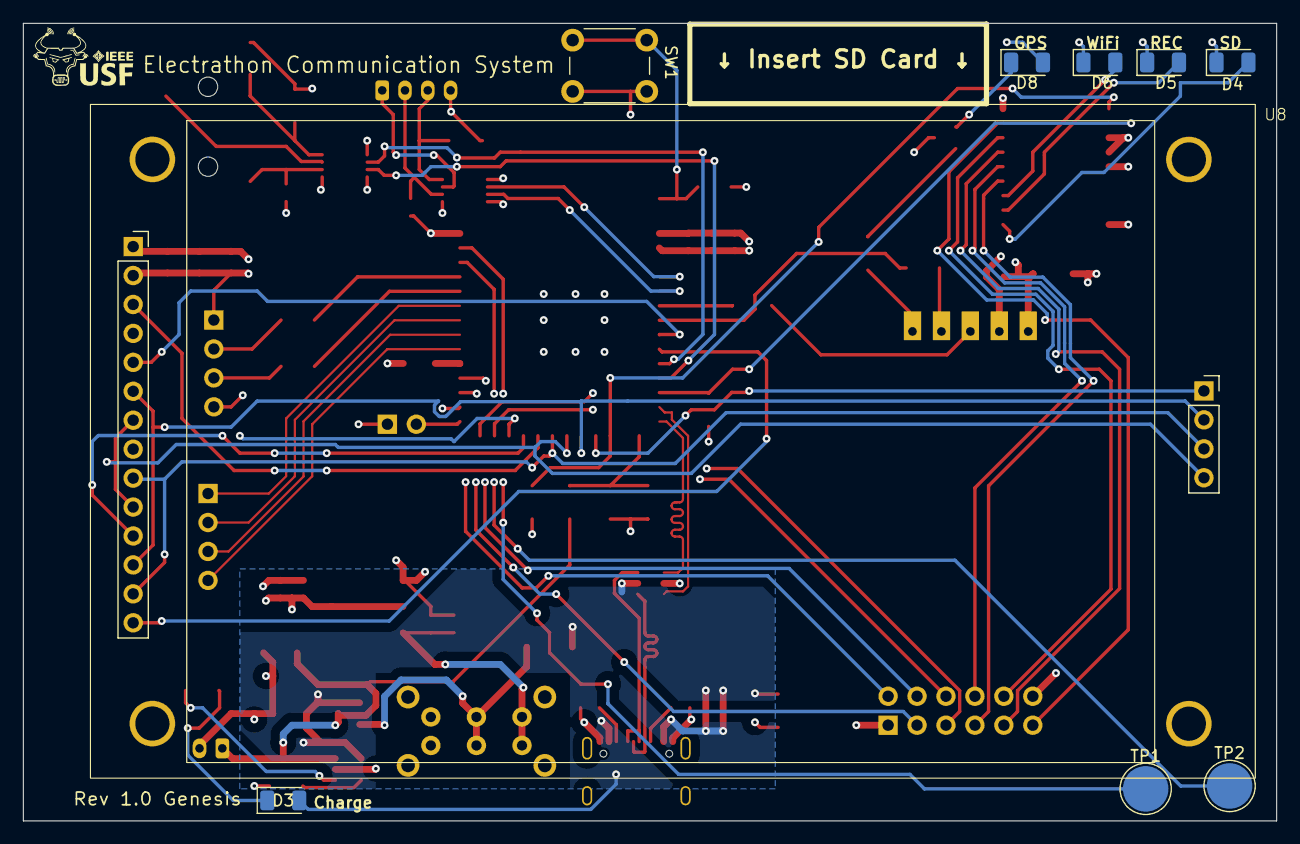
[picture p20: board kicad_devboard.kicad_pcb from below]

Board: 4 copper layers, 110.0 x 70.0 mm, 65 parts (9 on the bottom side), 70 nets.

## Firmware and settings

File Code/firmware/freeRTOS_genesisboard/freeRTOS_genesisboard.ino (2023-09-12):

#include "Definitions.h" //Contains Global Variables
#include "GPS_task.h" //Contains GPS functions
#include "LCD_task.h" //Responsible for LCD display
#include "DATA_task.h" //Responsible keep track of data and logging to SD Card
#include "WIRELESS_task.h" //Responsible for communicating to base station

bool dataActive = false;

static TaskHandle_t taskDATA = NULL; 

void setup() {
  Serial.begin(115200); // Debug serial port
  setupGPS();
  setupLCD();

  // xTaskCreatePinnedToCore(  // Use xTaskCreate() in vanilla FreeRTOS
  //             loopGPS,  // Function to be called
  //             "Update GPS Values",   // Name of task
  //             1024,         // Stack size (bytes in ESP32, words in FreeRTOS)
  //             NULL,         // Parameter to pass to function
  //             2,            // Task priority (0 to configMAX_PRIORITIES - 1) //Higher number = more priority
  //             NULL,         // Task handle
  //             1);     // Run on one core for demo purposes (ESP32 only)

  xTaskCreatePinnedToCore(loopGPS, "Update GPS", 1024, NULL, 2, NULL, 1);
  xTaskCreatePinnedToCore(loopDATA, "starts datalog", 10240, NULL, 4, &taskDATA, 1);
  xTaskCreatePinnedToCore(updateLCD, "Send screen to LCD", 4096, NULL, 1, NULL, 0); //RUNS ON SECOND CORE :)))
}

void loop() {
  checkTouchPin();
  vTaskDelay(50 / portTICK_PERIOD_MS); //Check button every 50 milliseconds
}

void checkTouchPin() {
  if (touchRead(1) < 35) {
    dataActive = !dataActive;
    if (dataActive) {
      vTaskResume(taskDATA);
    }
    vTaskDelay(2000 / portTICK_PERIOD_MS);
  }
}

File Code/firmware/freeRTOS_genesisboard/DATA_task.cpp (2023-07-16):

#include "DATA_task.h"
#include "SDscript.h"
hw_timer_t * timer = NULL;


//DATA Task should start after being called by either physical button or touchscreen
//For future, would like to add auto start using car velocity

int dateANDtime[6]; //Date and time arrray, (30, 24, 15, 17, 1, 2021);  // 17th Jan 2021 15:24:30
ESP32Time rtc(-18000);
double dataTime = 0.0;

//decodetime horrible method to get time
//replace with void crack_datetime(int *year, byte *month, byte *day, 
//    byte *hour, byte *minute, byte *second, byte *hundredths = 0, unsigned long *fix_age = 0);
void decodeTime()
{
    //char pointer declaration
    char temp[7];
    char temp2[9]; //temp2 used for time
    //assig number as string in char pointer
    sprintf((char*)temp,"%lu", gps_date);

    

    //Shifts string 1 to the right, to fix format
    if (strlen(temp)==5) {
      for(int i=6; i>0; i--)
        temp[i] = temp[i-1];
      temp[0] = '0';
    }

    dateANDtime[3] = (temp[0] - 48) * 10 + (temp[1] - 48); //Day of Month
    dateANDtime[4] = (temp[2] - 48) * 10 + (temp[3] - 48); //Month
    dateANDtime[5] = (temp[4] - 48) * 10 + (temp[5] - 48) + 2000; //Year
    sprintf((char*)temp2,"%lu", gps_time);
    dateANDtime[0] = (temp2[0] - 48) * 10 + (temp2[1] - 48); //Hour of Day
    dateANDtime[1] = (temp2[2] - 48) * 10 + (temp2[3] - 48); //Minutes
    dateANDtime[2] = (temp2[4] - 48) * 10 + (temp2[5] - 48); //Seconds, don't need milliseconds

    Serial.println(dateANDtime[3]);
    Serial.println(dateANDtime[4]);
    Serial.println(dateANDtime[5]);
    Serial.println("Time:");
    Serial.println(dateANDtime[0]);
    Serial.println(dateANDtime[1]);
    Serial.println(dateANDtime[2]);
}

void loopDATA(void *parameter) 
{
  SDsetup();
  // timer = timerBegin(0, 80, true);
  // timerStop(timer);
  while (1) {
    if (dataActive) {
      timer = timerBegin(0, 80, true);
      dataTime = timerReadSeconds(timer);
      updateTime();
      char filename[30];
      char dataEntry[40];
      //date is ddmmyy, time is hhmmss ms
      decodeTime();
      sprintf(filename, "/%lu.%lu.csv", gps_date, gps_time-4000000); //-4000000 to adjust time to Eastern Time
      //rtc.setTime(30, 24, 15, gps_date, 1, 2021);
      Serial.println(filename);


      rtc.setTime(dateANDtime[2], dateANDtime[1], dateANDtime[0], dateANDtime[3], dateANDtime[4], dateANDtime[5]);

      listDir(SD, "/", 0);

      writeFile(SD, filename, "# RaceRender Data\n");
      appendFile(SD, filename, "Time,Lap,Latitude,Longitude,MPH\n");

      while (dataActive) {
        sprintf(dataEntry, "%lf,0,%.6f,%.6f,0\n", dataTime, latitude, longitude);
        appendFile(SD, filename, dataEntry);
        dataTime = timerReadSeconds(timer);
        vTaskDelay(200 / portTICK_PERIOD_MS);
        // Serial.println(rtc.getTime("%A, %B %d %Y %H:%M:%S")); 
      }
      timerStop(timer);
    }
  //END OF LOOP, loop ending, save data below and suspend task until called again
  // timerRestart(timer);

  vTaskSuspend(NULL); //NULL means task suspends itself
  }
}

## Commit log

2023-06-09 Added Schematic Files and Arduino Code
    [Configuring options.txt, partitions.csv]
2023-06-09 Selected wrong out of date directory in previous commit
    [3.5 TFI SPI 480X320 V1 v3.step, Configuring options.txt, devboard.kicad_pcb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]
2023-06-09 created finalboard kicad file with esp32 chip, configured footprints&symbol for esp32s3 1u
    [ESP32-S3-WROOM-1U.STEP, finalboard.kicad_pcb, finalboard.kicad_sch]
2023-06-10 Added ESP NOW arduino tests
2023-06-10 Added GPS unit tests using software serial
    ESP32 has 3 UART's, 1 of them is for flashing and debugging. Electrathon car has bms which communicates through UART and cycle analyst also UART. Software Serial allows esp32 to communicate to UART d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
2023-07-01 freertos arduino
    freertos examples with screen & gps
2023-07-02 FinalBoard Changes
    [finalboard.kicad_pcb, finalboard.kicad_sch]
2023-07-02 Added Data Task
    To log data, keep track of time
2023-07-08 Added ESP32Time Library
    To load time into RTC
    Also added RTC test example using -5 GMT offset time
2023-07-11 Test using prototype data
    https://youtu.be/UrNn4R37eiI
    [100723.490500.csv]
2023-07-11 Design Iterations
    added touch buttons
    wired SPI sdcard and display
    [finalboard.kicad_pcb, finalboard.kicad_sch]
2023-07-16 Improved Data Accuracy and GPS sample
    -Changed SD to append every 200 ms instead of every 100 ms
    -Changed GPS sample rate to every 1 sec instead of 10 seconds
    -Instead of relying on delays to keep track of time, use hardware timer to keep track of exact time and not lose sync
2023-07-16 Time Tests
    using hardware timer of esp32
2023-08-07 Added Components
    added lipo charger, regulator, removed type B usb, added 3d Models
    [CUI_DEVICES_SJ-43515RS-SMT-TR.step, CUI_DEVICES_UJ2-BH-1-TH.step, GT-U7GpsModule v1.step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]
2023-08-10 Incorporated Feedback
    [finalboard.kicad_pcb, finalboard.kicad_sch]
2023-08-10 Schematic Mostly Done
    check esp32 pins
    [finalboard.kicad_pcb, finalboard.kicad_sch]
2023-08-12 Fixed Footprints, connected all nets
    [PI4ULS5V202UEX.step, PI4ULS5V202XVEX.step, finalboard.kicad_pcb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]
2023-08-18 routing initial
    [CUI_DEVICES_SJ-43514-SMT-TR.step, CUI_DEVICES_SJ-43515RS-SMT-TR.step, CUI_DEVICES_UJ2-BH-1-TH.step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]
2023-08-20 Update TFT_eSPI.zip
    Updated header config, if config is not correct wrong pins will be used, wrong colors displayed, wrong display driver
2023-09-02 pcb made genesis 1.0
    pcb made and manufactured
    [USB4105-GF-A.step, finalboard.kicad_pcb]
2023-09-12 Reorganized for public, genesis1.0board info
    [devboard.kicad_pcb, devboard.kicad_sch, finalboard.kicad_pcb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]
2023-09-13 Added settings for genesis board
    to get serial data communicating and utilize storage space
2024-01-26 code
    switched begin activation to boot button
    added cycle analyst task.cpp
    removements in lcd task
2024-02-05 Fixed Bug of Stop Recording and CSV log file
    dataentry variable needed to be bigger
    data entry task moved to other core, hardware timer would keep messing up when cycle analyst was read
